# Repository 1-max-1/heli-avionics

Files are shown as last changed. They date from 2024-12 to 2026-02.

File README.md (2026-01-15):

# heli-avionics
This repository contains the electronics and software for a flight controller. This controller is designed to run a coaxial helicopter using brushed DC motors. The board contains an rf transciever chip for wireless communication with a remote.

I had to learn alot for this project, as there were several things I had no experience with such as the radio transceiver circuitry. In the end, it turned out well and was very fun to make.

Description

Description

# PCBWay
The PCB was fabricated and assembled by [PCBWay](https://www.pcbway.com/). I’m impressed with how it turned out, and I’ve written a short review below based on my experience working with them.

#### PCB Quality
The finished PCB looks and feels excellent. The boards appear durable and well-made, with solid electrical connectivity throughout. Silkscreen print is sharp and clear, and the overall finish gives off a professional feel.

#### Assembly Quality
Assembly was just as good. All components were placed with precision, aligned nicely with their pads, and the soldering was clean — no excess, no bridges, and everything stayed neatly within the boundaries.

#### Communication & Support
Working with PCBWay was a smooth experience. They were professional and quick to respond to any questions I had. One thing I really appreciated was their communication before making any key decisions. For example:
- They double-checked with me before sourcing alternative components.
- When a part was unavailable, they suggested alternatives instead of just swapping it.
- After assembly, the quality control team contacted me about the orientation of a particular component, just to be sure, as the markings were slightly ambiguous.

#### Pricing & Turnaround
Pricing was fair, especially considering the quality and the support included. Quoting and sourcing components was made easy — PCBWay handled that for me, which saved a lot of time. Once everything was confirmed, shipping was fast and the boards arrived well-packed.

Overall, I'm happy with the result and wouldn’t hesitate to use PCBWay again in future projects. If you’re looking for a PCB manufacturer that’s reliable, responsive, and produces high-quality results — they’re worth checking out.

# Electronics
**Motor drivers**

The system uses three `DRV8212` BDC motor drivers to drive the tail and coaxial propellors. Some analysis shows that these chips should handle the current demands while remaining below maximum safe temperatures.
The motor driver circuit also includes significant bulk capacitance to handle large spikes in motor current.

The first design of the motor driver circuit used 1 driver chip for both motors. However after more testing, I found that the motors drew more current than expected when at full power. This was over the maximum limit of the motor driver chip. Initially, I started looking for replacement chips with better capabilities. However, the options were either too big, unavailable or could not operate at the voltage I wanted. Eventually, I realised this was the wrong way to go about it and decided to have another look at the original drivers. I discovered that if the 2 outputs on the chip were joined together, this would effectively double the maximum current, which was now sufficient for these motors. However, this solution does require 2 driver chips instead of one. I initially had concerns about space on the board, but after many hours of rearranging and rerouting I found a way to fit both parts on the board.

**MCU**

The MCU is an `atmega4808`. Although possibly not the fanciest choice, I selected this one because it's easy to program, I have used it before, and I know how to make it work.

**Programming**

The MCU can be programmed through UPDI or through the USART pins (once the bootloader has been uploaded). These are broken out to pin headers for easy access. The board also includes an external reset line + button.

I have also broken out an I2C line and a spare GPIO to another pin header in case I want to add more things onto the helicopter in the future.

**Radio**

This board includes a rf transceiver: `nrf24l01`. Like the MCU, this is not fancy but there's alot of documentation for it and I'd rather start with something easier because my rf knowledge is limited (for now).
The board contains an impedance matching network to match the transceiver output to 50 ohms. A wire antenna is used because it should give the best range and I dont have space for a PCB antenna or any bulky connectors like SMA. The antenna will also have to be tuned by cutting it to a specific length. I think UC has network analyzers which could help with this...

**Power regulation**

There are two seperate `TPS7A2030` voltage regulators - one for the radio and one for the rest of the circuit. This is done to try and minimize noise on the radio. The MCU also keeps track of the battery voltage through a divider to ensure that it remains at a safe level.

**Sensors**

The board includes a `BMP390` pressure sensor which can be used to determine the altitude of the helicopter.

# Software
TODO

Will use platformIO, c++

# Why?
I found this helicopter in an e-waste center. The remote was missing and the electronics inside of it seemed to be slightly burnt. 

| Description | 
|:--:| 
| *Disassembled helicopter on test stand* |

After taking it apart and relubricating all the shafts and gears, I tested the motors and they still seemed to work fine.
I decided it would be fun to fix it up and make my own controller for it.

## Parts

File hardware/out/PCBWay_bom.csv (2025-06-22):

Designator | Quantity | Value | Footprint | Package | MPN | DNP | Mount_Type | Description | LCSC Part #
C1, C15, C16, C17, C18, C19, C2, C20, C21, C22, C25, C26, C30, C31, C4, C5, C6 | 17 | 22uF | C_0603_1608Metric_Pad1.08x0.95mm_HandSolder |  | CL10A226MQ8NRNC |  | smt | 6.3V 22uF X5R ±20% 0603 Multilayer Ceramic Capacitors MLCC - SMD/SMT ROHS | C59461
C10 | 1 | 2.2nF | C_0603_1608Metric_Pad1.08x0.95mm_HandSolder |  | 0603B222K500NT |  | smt | 50V 2.2nF X7R ±10% 0603 Multilayer Ceramic Capacitors MLCC - SMD/SMT ROHS | C1604
C11, C9 | 2 | 12pF | C_0603_1608Metric_Pad1.08x0.95mm_HandSolder |  | CC0603FRNPO9BN120 |  | smt | 50V 12pF NP0 ±1% 0603 Multilayer Ceramic Capacitors MLCC - SMD/SMT ROHS | C519482
C12 | 1 | 4.7pF | C_0603_1608Metric_Pad1.08x0.95mm_HandSolder |  | 0603CG4R7C500NT |  | smt | 50V 4.7pF C0G 0603 Multilayer Ceramic Capacitors MLCC - SMD/SMT ROHS | C1669
C13 | 1 | 1.5pF | C_0603_1608Metric_Pad1.08x0.95mm_HandSolder |  | HH18N1R5B500CT |  | smt | 1.5 pF ±0.1pF 50V Ceramic Capacitor C0G, NP0 0603 (1608 Metric)
C14 | 1 | 1pF | C_0603_1608Metric_Pad1.08x0.95mm_HandSolder |  | HH18N1R0B500CT |  | smt | 1 pF ±0.1pF 50V Ceramic Capacitor C0G, NP0 0603 (1608 Metric)
C27 | 1 | 1nF | C_0603_1608Metric_Pad1.08x0.95mm_HandSolder |  | CL10B102KB8NNNC | Yes | smt | 50V 1nF X7R ±10% 0603 Multilayer Ceramic Capacitors MLCC - SMD/SMT ROHS | C1588
C28 | 1 | 100nF | C_0603_1608Metric_Pad1.08x0.95mm_HandSolder |  | CC0603KRX7R9BB104 |  | smt | 50V 100nF X7R ±10% 0603 Multilayer Ceramic Capacitors MLCC - SMD/SMT ROHS | C14663
C3 | 1 | 100nF | C_0603_1608Metric_Pad1.08x0.95mm_HandSolder |  | CC0603KRX7R9BB104 | Yes | smt | 50V 100nF X7R ±10% 0603 Multilayer Ceramic Capacitors MLCC - SMD/SMT ROHS | C14663
C7 | 1 | 33nF | C_0603_1608Metric_Pad1.08x0.95mm_HandSolder |  | CL10B333KB8NNNC |  | smt | 50V 33nF X7R ±10% 0603 Multilayer Ceramic Capacitors MLCC - SMD/SMT ROHS | C21117
C8 | 1 | 10nF | C_0603_1608Metric_Pad1.08x0.95mm_HandSolder |  | 0603B103K500NT | Yes | smt | Unpolarized capacitor | C57112
D2 | 1 | NCD0805R1 | LED_0805_2012Metric_Pad1.15x1.40mm_HandSolder |  | NCD0805R1 |  | smt | Red 25mA 67mcd~195mcd -30℃~+85℃ 615nm~630nm Independent Diode Red 130° 65mW 1.6V~2.6V 0805 LED Indication - Discrete ROHS | C84256
L1 | 1 | 2.7nH | L_0603_1608Metric_Pad1.05x0.95mm_HandSolder |  | BSCQ000603032N7B00 |  | smt | 2.7 nH Unshielded Multilayer Inductor 400 mA 320mOhm Max 0201 (0603 Metric)
L2 | 1 | 8.2nH | L_0603_1608Metric_Pad1.05x0.95mm_HandSolder |  | BSCQ000603038N2H00 |  | smt | 8.2 nH Unshielded Multilayer Inductor 290 mA 570mOhm Max 0201 (0603 Metric)
L3 | 1 | 3.9nH | L_0603_1608Metric_Pad1.05x0.95mm_HandSolder |  | BSCQ000603033N9B00 |  | smt | 3.9 nH Unshielded Multilayer Inductor 350 mA 410mOhm Max 0201 (0603 Metric)
Q1 | 1 | AO3400A | SOT-23 |  | AO3400A |  | smt | 30V Vds, 5.7A Id, N-Channel MOSFET, SOT-23 | C20917
R1 | 1 | 33k | R_0603_1608Metric_Pad0.98x0.95mm_HandSolder |  | 0603WAF3302T5E |  | smt | 100mW Thick Film Resistors 75V ±100ppm/℃ ±1% 33kΩ 0603 Chip Resistor - Surface Mount ROHS | C4216
R10 | 1 | 100R | R_0805_2012Metric_Pad1.20x1.40mm_HandSolder |  | 0805W8F1000T5E |  | smt | 125mW Thick Film Resistors 150V ±100ppm/℃ ±1% 100Ω 0805 Chip Resistor - Surface Mount ROHS | C17408
R11 | 1 | 470R | R_0603_1608Metric_Pad0.98x0.95mm_HandSolder |  | 0603WAF4700T5E |  | smt | 100mW Thick Film Resistors 75V ±100ppm/℃ ±1% 470Ω 0603 Chip Resistor - Surface Mount ROHS | C23179
R12, R13 | 2 | 4k7 | R_0603_1608Metric_Pad0.98x0.95mm_HandSolder |  | 0603WAF4701T5E |  | smt | 100mW Thick Film Resistors 75V ±100ppm/℃ ±1% 4.7kΩ 0603 Chip Resistor - Surface Mount ROHS | C23162
R2 | 1 | 330R | R_0603_1608Metric_Pad0.98x0.95mm_HandSolder |  | 0603WAF3300T5E |  | smt | 100mW Thick Film Resistors 75V ±100ppm/℃ ±1% 330Ω 0603 Chip Resistor - Surface Mount ROHS | C23138
R3, R5, R6 | 3 | 22k | R_0603_1608Metric_Pad0.98x0.95mm_HandSolder |  | 0603WAF2202T5E |  | smt | 100mW Thick Film Resistors 75V ±100ppm/℃ ±1% 22kΩ 0603 Chip Resistor - Surface Mount ROHS | C31850
R4 | 1 | 1M | R_0603_1608Metric_Pad0.98x0.95mm_HandSolder |  | 0603WAF1004T5E |  | smt | 100mW Thick Film Resistors 75V ±100ppm/℃ ±1% 1MΩ 0603 Chip Resistor - Surface Mount ROHS | C22935
R7 | 1 | 150R | R_0603_1608Metric_Pad0.98x0.95mm_HandSolder |  | 0603WAF1500T5E |  | smt | 100mW Thick Film Resistors 75V ±100ppm/℃ ±1% 150Ω 0603 Chip Resistor - Surface Mount ROHS | C22808
R8 | 1 | 51k | R_0603_1608Metric_Pad0.98x0.95mm_HandSolder |  | 0603WAF5102T5E |  | smt | 100mW Thick Film Resistors 75V ±100ppm/℃ ±1% 51kΩ 0603 Chip Resistor - Surface Mount ROHS | C23196
R9 | 1 | 68R | R_0805_2012Metric_Pad1.20x1.40mm_HandSolder |  | 0805W8F680JT5E |  | smt | 125mW Thick Film Resistors 150V ±1% ±200ppm/℃ 68Ω 0805 Chip Resistor - Surface Mount ROHS | C17802
SW1 | 1 | Reset | SW_Push_SPST_NO_Alps_SKRK |  | SKRKAEE020 |  | smt | 2.9mm 2mm Round Button 50mA Vertical welding 3.9mm SPST 12V SMD Tactile Switches ROHS | C115357
U1 | 1 | ATmega4808-A | TQFP-32_7x7mm_P0.8mm |  | ATMEGA4808-AFR |  | smt | AVR Microcontroller, 20MHz, 48kB Flash, 6kB SRAM, 256B EEPROM, TQFP-32 | C2052755
U2 | 1 | NRF24L01P | QFN-20-1EP_4x4mm_P0.5mm_EP2.5x2.5mm |  | NRF24L01P-R |  | smt | Ultra low power 2 Mbps 2.4GHz RF Transceiver, QFN-20 | C8791
U3, U4, U8 | 3 | DRV8212 | WSON-8-1EP_2x2mm_P0.5mm_EP0.9x1.6mm_ThermalVias |  | DRV8212DSGR |  | smt | H-Bridge driver, 4A, Low Voltage, PWM input, Half Bridge Mode, Low-Power Sleep Mode, WSON-8 | C2843766
U5 | 1 | BMP390L | BMP390L LGA 2.0x2.0 mm |  | BMP390L |  | smt | 24-bit barometric pressure sensor, low-noise, low-power. | C2684802
U6, U7 | 2 | TPS7A2030PDBV | SOT-23-5_HandSoldering |  | TPS7A2030PDBVR |  | smt | 300-mA Ultra-Low-Noise Low-IQ, High PSRR LDO, 3.0V, SOT-23 | C963429
Y1 | 1 | 16MHz | Crystal_SMD_3225-4Pin_3.2x2.5mm |  | X322516MLB4SI |  | smt | Four pin crystal, 16MHz, X322516MLB4SI | C13738

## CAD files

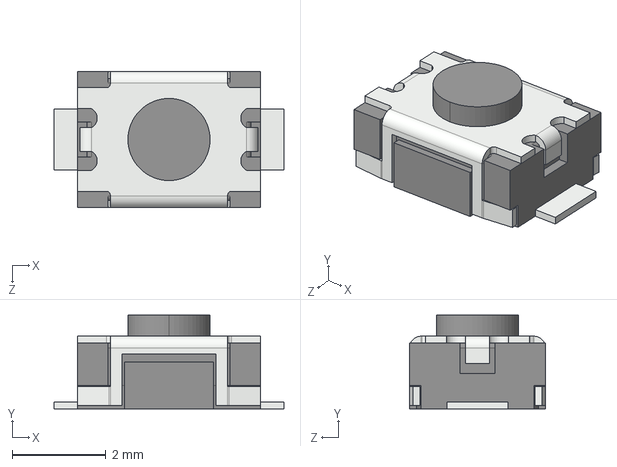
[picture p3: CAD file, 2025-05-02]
hardware/heli-3d-models/User Library-Pushbutton3x4x2.step
4.90 x 2.00 x 2.90 mm

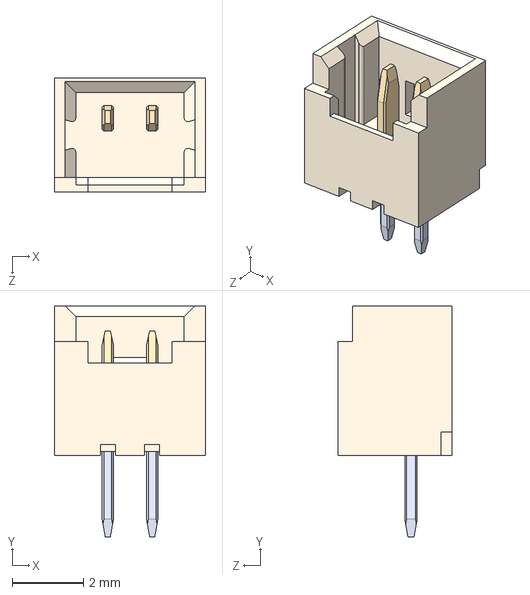
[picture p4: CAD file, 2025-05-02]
hardware/heli-3d-models/molex-picoblade-2pin-1.25mm-pitch.STEP
4.25 x 6.50 x 3.20 mm

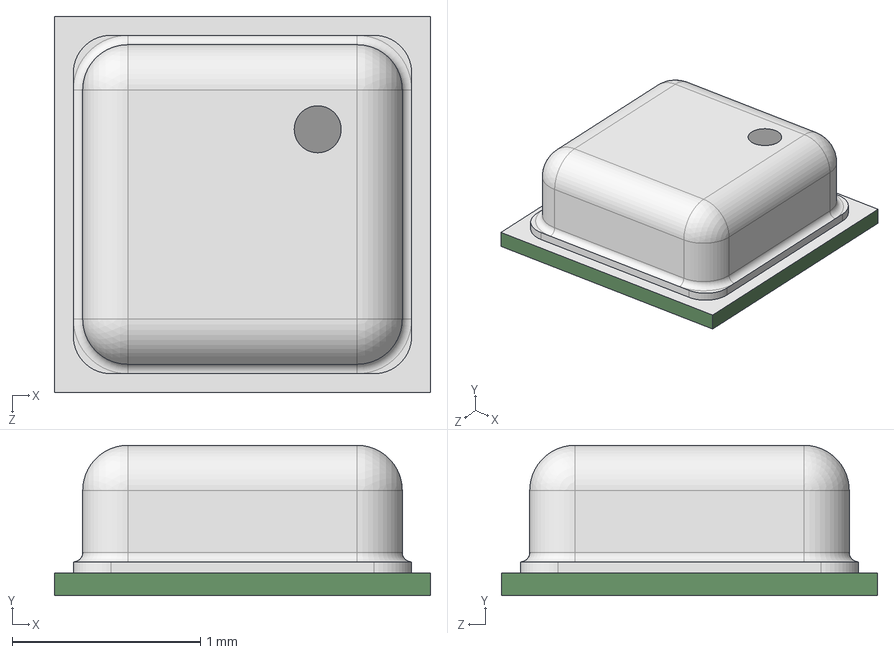
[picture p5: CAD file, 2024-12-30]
hardware/heli-3d-models/BMP390L.step
2.00 x 0.8 x 2.00 mm

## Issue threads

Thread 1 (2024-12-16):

Notes

1-max-1, 2024-12-16:
### MCU
Looking at atmega4809. I have experience with this already, programming it is fairly easy. It has SPI, I2C and PWM so should be good.
Flash size should be enough. Bootloaders are simple. Plenty of decoupling.

### RF
Will be wired to nrf24 chip. Schematic for this can be found in datasheets and there are plenty of examples online, including the PCB antenna and impedance matching network.

### Motor drivers
Brushed, DC, x3. Drive through PWM. Could use motor driver chip, or mosfets directly.

### Altitude sensor
Some kind of pressure sensor, preferably over SPI.

### Battery
Powered by lipo cells, may need 2 to run the motors properly, however nrf24 runs on 3.3v so would need LDO.
Also need battery monitoring system to avoid using the cells when below safe threshold. No onboard battery charging system due to complexity and fire hazard.

1-max-1, 2025-01-15:
TODO:

- [ ] 2x LED's on GPIO pins, not power (always on) because waste of current. Maybe one on the bootloader pin.
- [ ] Check pin order on connectors
- [ ] Check footprints and pin order on all components
- [ ] UART programming
- [ ] Spare exposed GPIO and SPI
- [ ] Exposed pad/hole for additional decoupling to be added if needed.
- [ ] Antenna

1-max-1, 2025-05-31:
### RF components
**1.5pF cap**
LCSC: [C3869699](https://www.lcsc.com/product-detail/Multilayer-Ceramic-Capacitors-MLCC-SMD-SMT_Murata-Electronics-GQM1875C2E1R5BB12D_C3869699.html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)

**1 pF cap**
LCSC: [C2178951](https://www.lcsc.com/product-detail/Multilayer-Ceramic-Capacitors-MLCC-SMD-SMT_Murata-Electronics-GQM1875C2E1R0BB12D_C2178951.html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)

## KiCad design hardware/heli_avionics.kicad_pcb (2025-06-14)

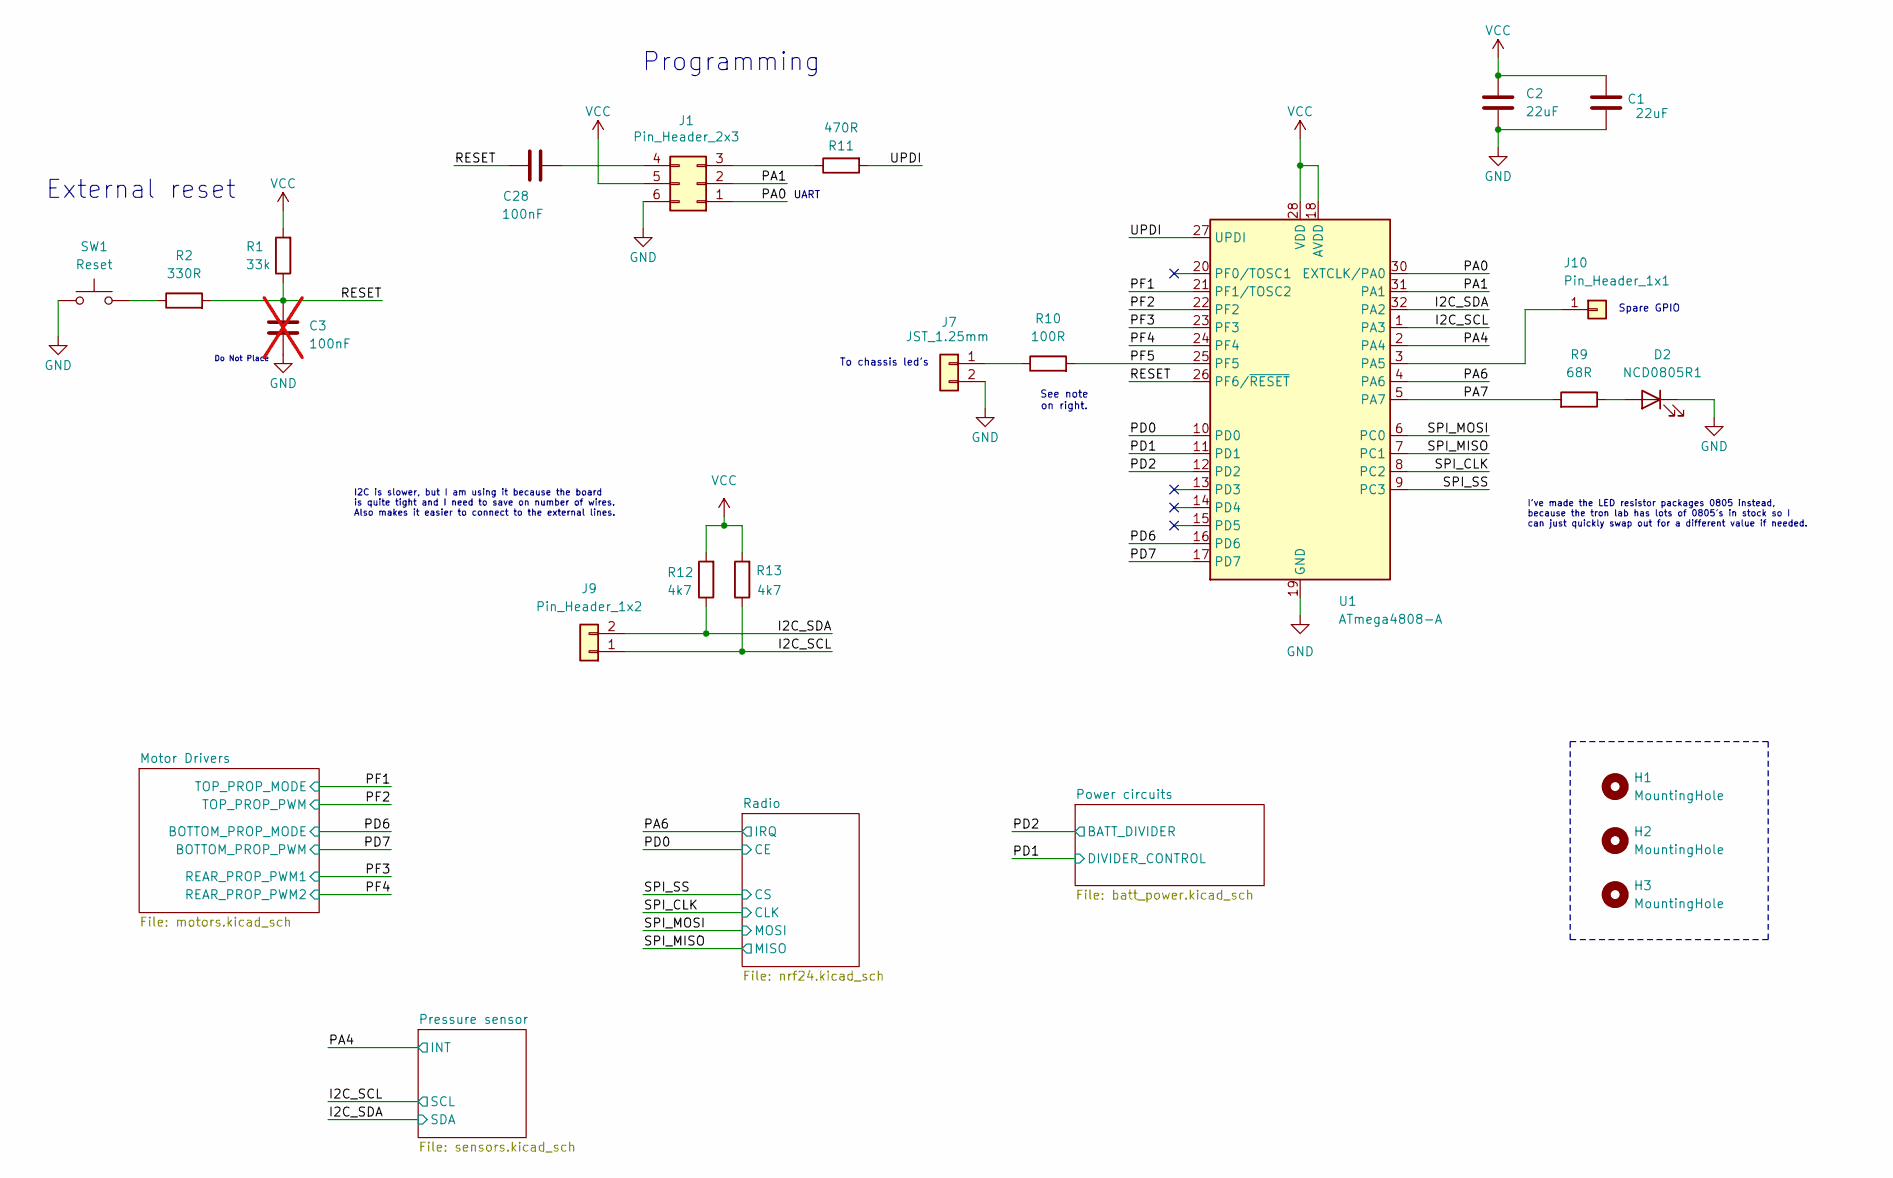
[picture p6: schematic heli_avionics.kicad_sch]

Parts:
C1, C2: 22uF; C_0603_1608Metric_Pad1.08x0.95mm_HandSolder; MPN CL10A226MQ8NRNC; LCSC Part # C59461
C3: 100nF; C_0603_1608Metric_Pad1.08x0.95mm_HandSolder; MPN CC0603KRX7R9BB104; LCSC Part # C14663; not fitted
C28: 100nF; C_0603_1608Metric_Pad1.08x0.95mm_HandSolder; MPN CC0603KRX7R9BB104; LCSC Part # C14663
D2: NCD0805R1; LED_0805_2012Metric_Pad1.15x1.40mm_HandSolder; MPN NCD0805R1; LCSC Part # C84256
H1, H2, H3: MountingHole; MountingHole_2mm
J1: Pin_Header_2x3; PinHeader_2x03_P2.54mm_Vertical
J7: JST_1.25mm; Molex_PicoBlade_53047-0210_1x02_P1.25mm_Vertical
J9: Pin_Header_1x2; PinHeader_1x02_P2.54mm_Vertical
J10: Pin_Header_1x1; PinHeader_1x01_P2.54mm_Vertical
R1: 33k; R_0603_1608Metric_Pad0.98x0.95mm_HandSolder; MPN 0603WAF3302T5E; LCSC Part # C4216
R2: 330R; R_0603_1608Metric_Pad0.98x0.95mm_HandSolder; MPN 0603WAF3300T5E; LCSC Part # C23138
R9: 68R; R_0805_2012Metric_Pad1.20x1.40mm_HandSolder; MPN 0805W8F680JT5E; LCSC Part # C17802
R10: 100R; R_0805_2012Metric_Pad1.20x1.40mm_HandSolder; MPN 0805W8F1000T5E; LCSC Part # C17408
R11: 470R; R_0603_1608Metric_Pad0.98x0.95mm_HandSolder; MPN 0603WAF4700T5E; LCSC Part # C23179
R12, R13: 4k7; R_0603_1608Metric_Pad0.98x0.95mm_HandSolder; MPN 0603WAF4701T5E; LCSC Part # C23162
SW1: Reset; SW_Push_SPST_NO_Alps_SKRK; MPN SKRKAEE020; LCSC Part # C115357
U1: ATmega4808-A; TQFP-32_7x7mm_P0.8mm; MPN ATMEGA4808-AFR; LCSC Part # C2052755

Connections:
/I2C_SCL: J9.1, R13.1, U1.1 (PA3); also elsewhere on the board
/I2C_SDA: J9.2, R12.1, U1.32 (PA2); also elsewhere on the board
/PA0: J1.1, U1.30 (EXTCLK/PA0)
/PA1: J1.2, U1.31 (PA1)
/PA4: U1.2 (PA4); also elsewhere on the board
/PA6: U1.4 (PA6); also elsewhere on the board
/PA7: R9.2, U1.5 (PA7)
/PD0: U1.10 (PD0); also elsewhere on the board
/PD1: U1.11 (PD1); also elsewhere on the board
/PD2: U1.12 (PD2); also elsewhere on the board
/PD6: U1.16 (PD6); also elsewhere on the board
/PD7: U1.17 (PD7); also elsewhere on the board
/PF1: U1.21 (PF1/TOSC2); also elsewhere on the board
/PF2: U1.22 (PF2); also elsewhere on the board
/PF3: U1.23 (PF3); also elsewhere on the board
/PF4: U1.24 (PF4); also elsewhere on the board
/PF5: R10.2, U1.25 (PF5)
/RESET: C3.1, C28.1, R1.1, R2.2, U1.26 (PF6/~RESET)
/SPI_CLK: U1.8 (PC2); also elsewhere on the board
/SPI_MISO: U1.7 (PC1); also elsewhere on the board
/SPI_MOSI: U1.6 (PC0); also elsewhere on the board
/SPI_SS: U1.9 (PC3); also elsewhere on the board
/UPDI: R11.2, U1.27 (UPDI)
GND: C1.2, C2.2, C3.2, D2.1 (K), J1.6, J7.2, SW1.1, U1.19 (GND), U1.29 (GND); also elsewhere on the board
unnamed: D2.2 (A), R9.1
unnamed: J1.3, R11.1
unnamed: C28.2, J1.4
unnamed: J7.1, R10.1
unnamed: J10.1, U1.3 (PA5)
unnamed: R2.1, SW1.2
VCC: C1.1, C2.1, J1.5, R1.2, R12.2, R13.2, U1.18 (AVDD), U1.28 (VDD); also elsewhere on the board

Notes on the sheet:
Do Not Place
I've made the LED resistor packages 0805 instead, because the tron lab has lots of 0805's in stock so I can just quickly swap out for a different value if needed.
I2C is slower, but I am using it because the board is quite tight and I need to save on number of wires. Also makes it easier to connect to the external lines.
UART
See note on right.
To chassis led's
Spare GPIO
Programming
External reset

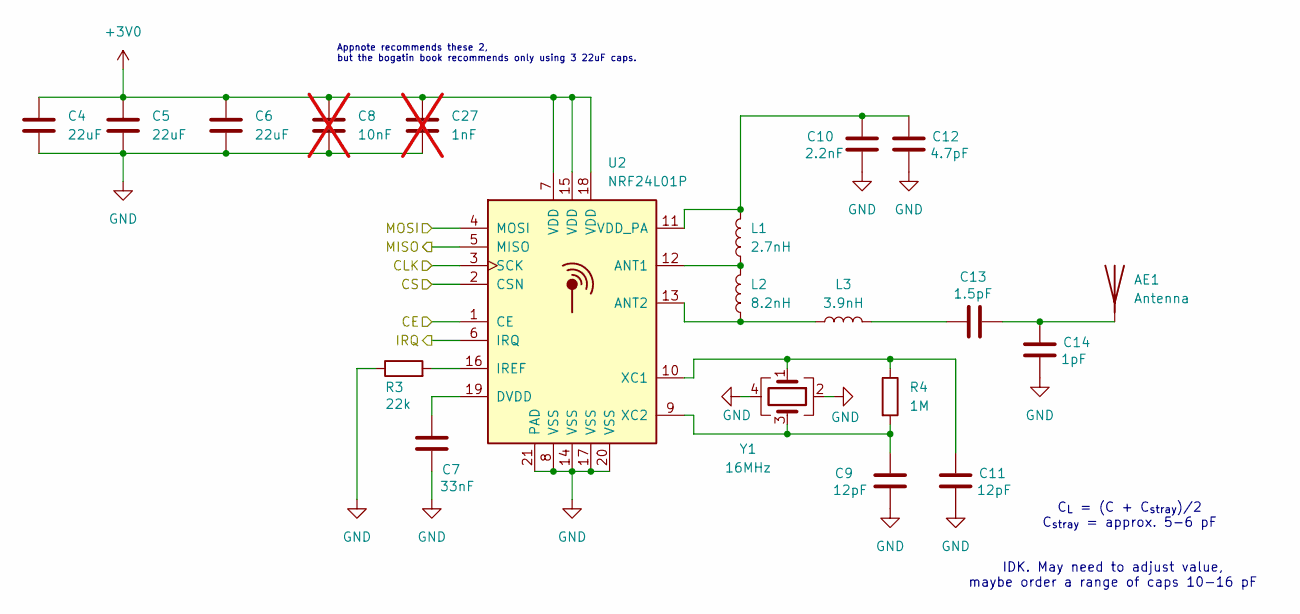
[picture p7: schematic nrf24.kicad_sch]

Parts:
AE1: Antenna; SolderWire-0.5sqmm_1x01_D0.9mm_OD2.1mm
C4, C5, C6: 22uF; C_0603_1608Metric_Pad1.08x0.95mm_HandSolder; MPN CL10A226MQ8NRNC; LCSC Part # C59461
C7: 33nF; C_0603_1608Metric_Pad1.08x0.95mm_HandSolder; MPN CL10B333KB8NNNC; LCSC Part # C21117
C8: 10nF; C_0603_1608Metric_Pad1.08x0.95mm_HandSolder; MPN 0603B103K500NT; LCSC Part # C57112; not fitted
C9, C11: 12pF; C_0603_1608Metric_Pad1.08x0.95mm_HandSolder; MPN CC0603FRNPO9BN120; LCSC Part # C519482
C10: 2.2nF; C_0603_1608Metric_Pad1.08x0.95mm_HandSolder; MPN 0603B222K500NT; LCSC Part # C1604
C12: 4.7pF; C_0603_1608Metric_Pad1.08x0.95mm_HandSolder; MPN 0603CG4R7C500NT; LCSC Part # C1669
C13: 1.5pF; C_0603_1608Metric_Pad1.08x0.95mm_HandSolder; MPN HH18N1R5B500CT
C14: 1pF; C_0603_1608Metric_Pad1.08x0.95mm_HandSolder; MPN HH18N1R0B500CT
C27: 1nF; C_0603_1608Metric_Pad1.08x0.95mm_HandSolder; MPN CL10B102KB8NNNC; LCSC Part # C1588; not fitted
L1: 2.7nH; L_0603_1608Metric_Pad1.05x0.95mm_HandSolder; MPN BSCQ000603032N7B00
L2: 8.2nH; L_0603_1608Metric_Pad1.05x0.95mm_HandSolder; MPN BSCQ000603038N2H00
L3: 3.9nH; L_0603_1608Metric_Pad1.05x0.95mm_HandSolder; MPN BSCQ000603033N9B00
R3: 22k; R_0603_1608Metric_Pad0.98x0.95mm_HandSolder; MPN 0603WAF2202T5E; LCSC Part # C31850
R4: 1M; R_0603_1608Metric_Pad0.98x0.95mm_HandSolder; MPN 0603WAF1004T5E; LCSC Part # C22935
U2: NRF24L01P; NRF24L01_HandSolder_SpecialPad; MPN NRF24L01P-R; LCSC Part # C8791
Y1: 16MHz; Crystal_SMD_3225-4Pin_3.2x2.5mm; MPN X322516MLB4SI; LCSC Part # C13738

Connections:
+3V0: C4.1, C5.1, C6.1, C8.1, C27.1, U2.7 (VDD), U2.15 (VDD), U2.18 (VDD); also elsewhere on the board
/PA6: U2.6 (IRQ); also elsewhere on the board
/PD0: U2.1 (CE); also elsewhere on the board
/SPI_CLK: U2.3 (SCK); also elsewhere on the board
/SPI_MISO: U2.5 (MISO); also elsewhere on the board
/SPI_MOSI: U2.4 (MOSI); also elsewhere on the board
/SPI_SS: U2.2 (CSN); also elsewhere on the board
GND: C4.2, C5.2, C6.2, C7.2, C8.2, C9.2, C10.2, C11.2, C12.2, C14.2, C27.2, R3.1, U2.8 (VSS), U2.14 (VSS), U2.17 (VSS), U2.20 (VSS), U2.21 (PAD), Y1.2, Y1.4; also elsewhere on the board
unnamed: AE1.1 (A), C13.2, C14.1
unnamed: C13.1, L3.2
unnamed: L1.1, L2.2, U2.12 (ANT1)
unnamed: L2.1, L3.1, U2.13 (ANT2)
unnamed: C7.1, U2.19 (DVDD)
unnamed: R3.2, U2.16 (IREF)
unnamed: C10.1, C12.1, L1.2, U2.11 (VDD_PA)
unnamed: C11.1, R4.1, U2.10 (XC1), Y1.1
unnamed: C9.1, R4.2, U2.9 (XC2), Y1.3

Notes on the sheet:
C_{L} = (C + C_{stray})/2 C_{stray} = approx. 5-6 pF
Appnote recommends these 2, but the bogatin book recommends only using 3 22uF caps.
IDK. May need to adjust value, maybe order a range of caps 10-16 pF

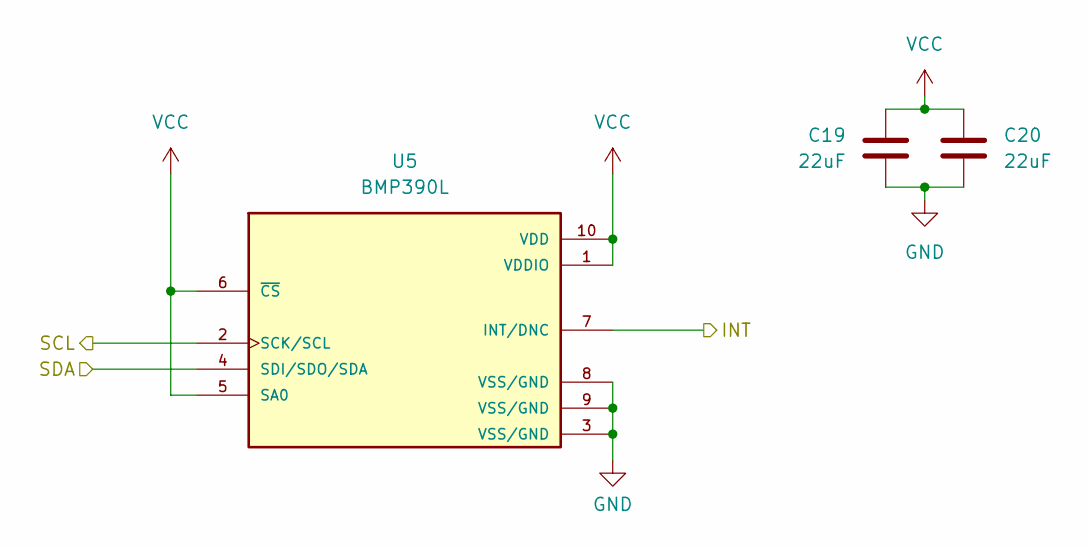
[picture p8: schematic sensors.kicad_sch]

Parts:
C19, C20: 22uF; C_0603_1608Metric_Pad1.08x0.95mm_HandSolder; MPN CL10A226MQ8NRNC; LCSC Part # C59461
U5: BMP390L; MPN BMP390L; LCSC Part # C2684802

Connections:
/I2C_SCL: U5.2 (SCK/SCL); also elsewhere on the board
/I2C_SDA: U5.4 (SDI/SDO/SDA); also elsewhere on the board
/PA4: U5.7 (INT/DNC); also elsewhere on the board
GND: C19.2, C20.2, U5.3 (VSS/GND), U5.8 (VSS/GND), U5.9 (VSS/GND); also elsewhere on the board
VCC: C19.1, C20.1, U5.1 (VDDIO), U5.5 (SA0), U5.6 (~CS), U5.10 (VDD); also elsewhere on the board

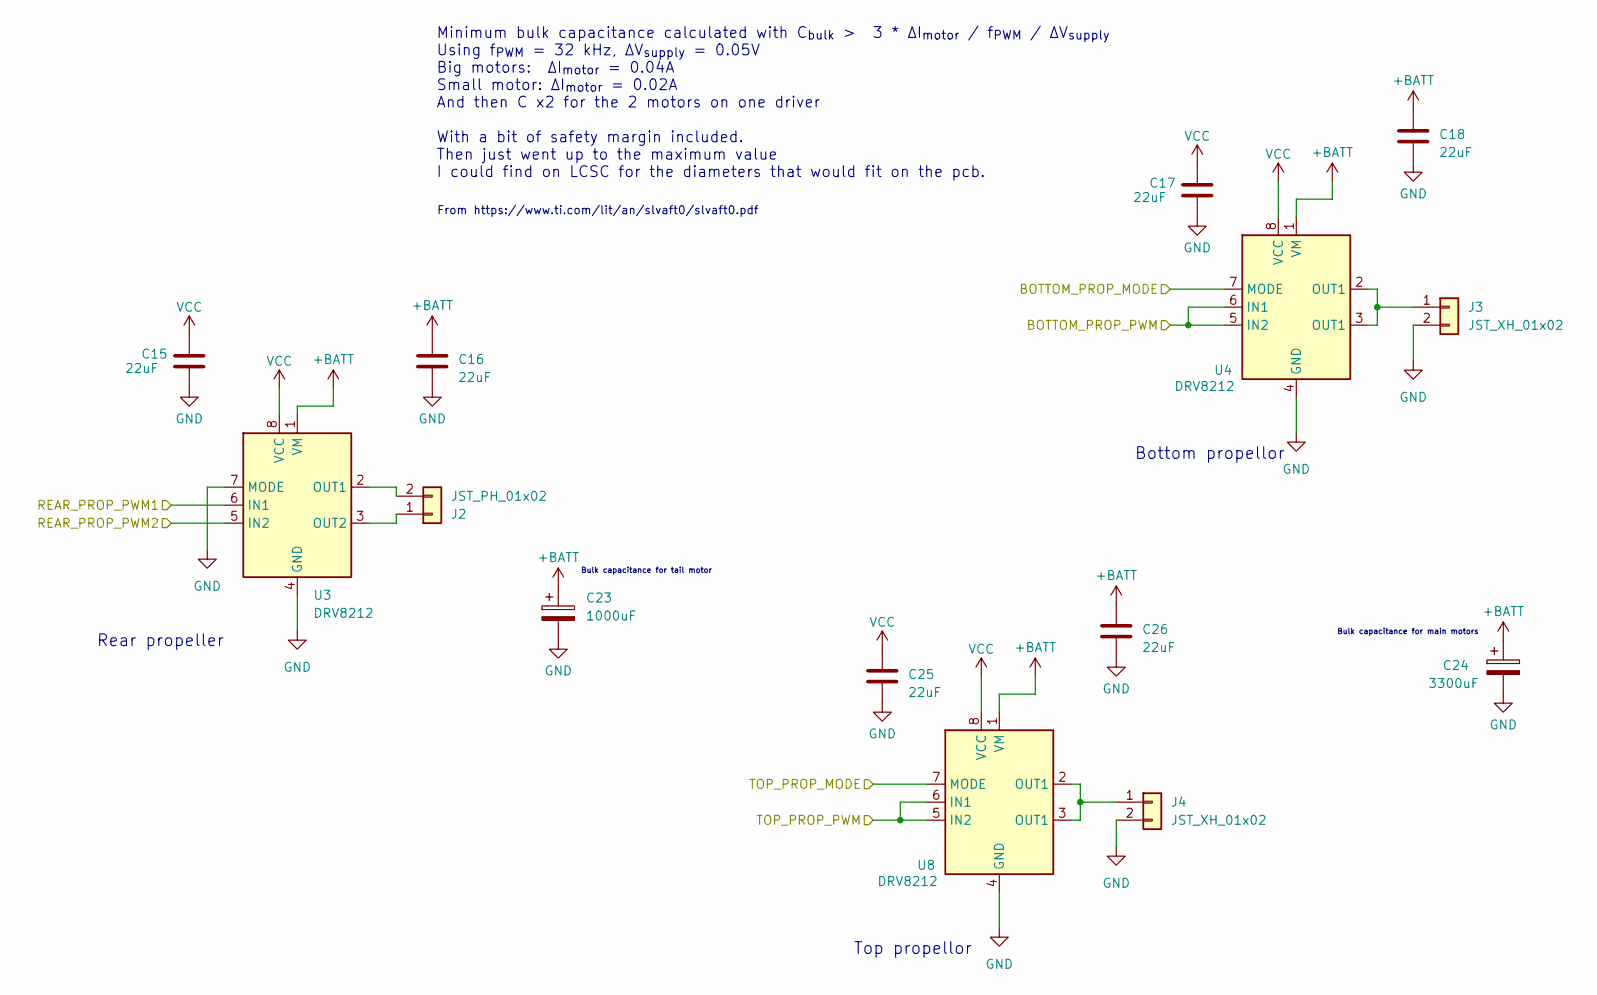
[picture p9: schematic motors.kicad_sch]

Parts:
C15, C16, C17, C18, C25, C26: 22uF; C_0603_1608Metric_Pad1.08x0.95mm_HandSolder; MPN CL10A226MQ8NRNC; LCSC Part # C59461
C23: 1000uF; CP_Radial_D6.3mm_P2.50mm; MPN SPT1AM102E14ORVZC; LCSC Part # C3024245
C24: 3300uF; CP_Radial_D10.0mm_P5.00mm; MPN RL1A332MG250A00CE0; LCSC Part # C240437
J2: JST_PH_01x02; JST_PH_B2B-PH-K_1x02_P2.00mm_Vertical
J3, J4: JST_XH_01x02; JST_XH_B2B-XH-A_1x02_P2.50mm_Vertical
U3, U4, U8: DRV8212; WSON-8-1EP_2x2mm_P0.5mm_EP0.9x1.6mm_ThermalVias; MPN DRV8212DSGR; LCSC Part # C2843766

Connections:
+BATT: C16.1, C18.1, C23.1, C24.1, C26.1, U3.1 (VM), U4.1 (VM), U8.1 (VM); also elsewhere on the board
/PD6: U4.7 (MODE); also elsewhere on the board
/PD7: U4.5 (IN2), U4.6 (IN1); also elsewhere on the board
/PF1: U8.7 (MODE); also elsewhere on the board
/PF2: U8.5 (IN2), U8.6 (IN1); also elsewhere on the board
/PF3: U3.6 (IN1); also elsewhere on the board
/PF4: U3.5 (IN2); also elsewhere on the board
GND: C15.2, C16.2, C17.2, C18.2, C23.2, C24.2, C25.2, C26.2, J3.2, J4.2, U3.4 (GND), U3.7 (MODE), U3.9 (GND), U4.4 (GND), U4.9 (GND), U8.4 (GND), U8.9 (GND); also elsewhere on the board
unnamed: J2.1, U3.3 (OUT2)
unnamed: J2.2, U3.2 (OUT1)
unnamed: J3.1, U4.2 (OUT1), U4.3 (OUT1)
unnamed: J4.1, U8.2 (OUT1), U8.3 (OUT1)
VCC: C15.1, C17.1, C25.1, U3.8 (VCC), U4.8 (VCC), U8.8 (VCC); also elsewhere on the board

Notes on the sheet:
Top propellor
Rear propeller
Minimum bulk capacitance calculated with C_{bulk} > 3 * ∆I_{motor} / f_{PWM} / ∆V_{supply} Using f_{PWM} = 32 kHz, ∆V_{supply} = 0.05V Big motors: ∆I_{motor} = 0.04A Small motor: ∆I_{motor} = 0.02A And then C x2 for the 2 motors on one driver With a bit of safety margin included. Then just went up 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
From https://www.ti.com/lit/an/slvaft0/slvaft0.pdf
Bulk capacitance for tail motor
Bottom propellor
Bulk capacitance for main motors

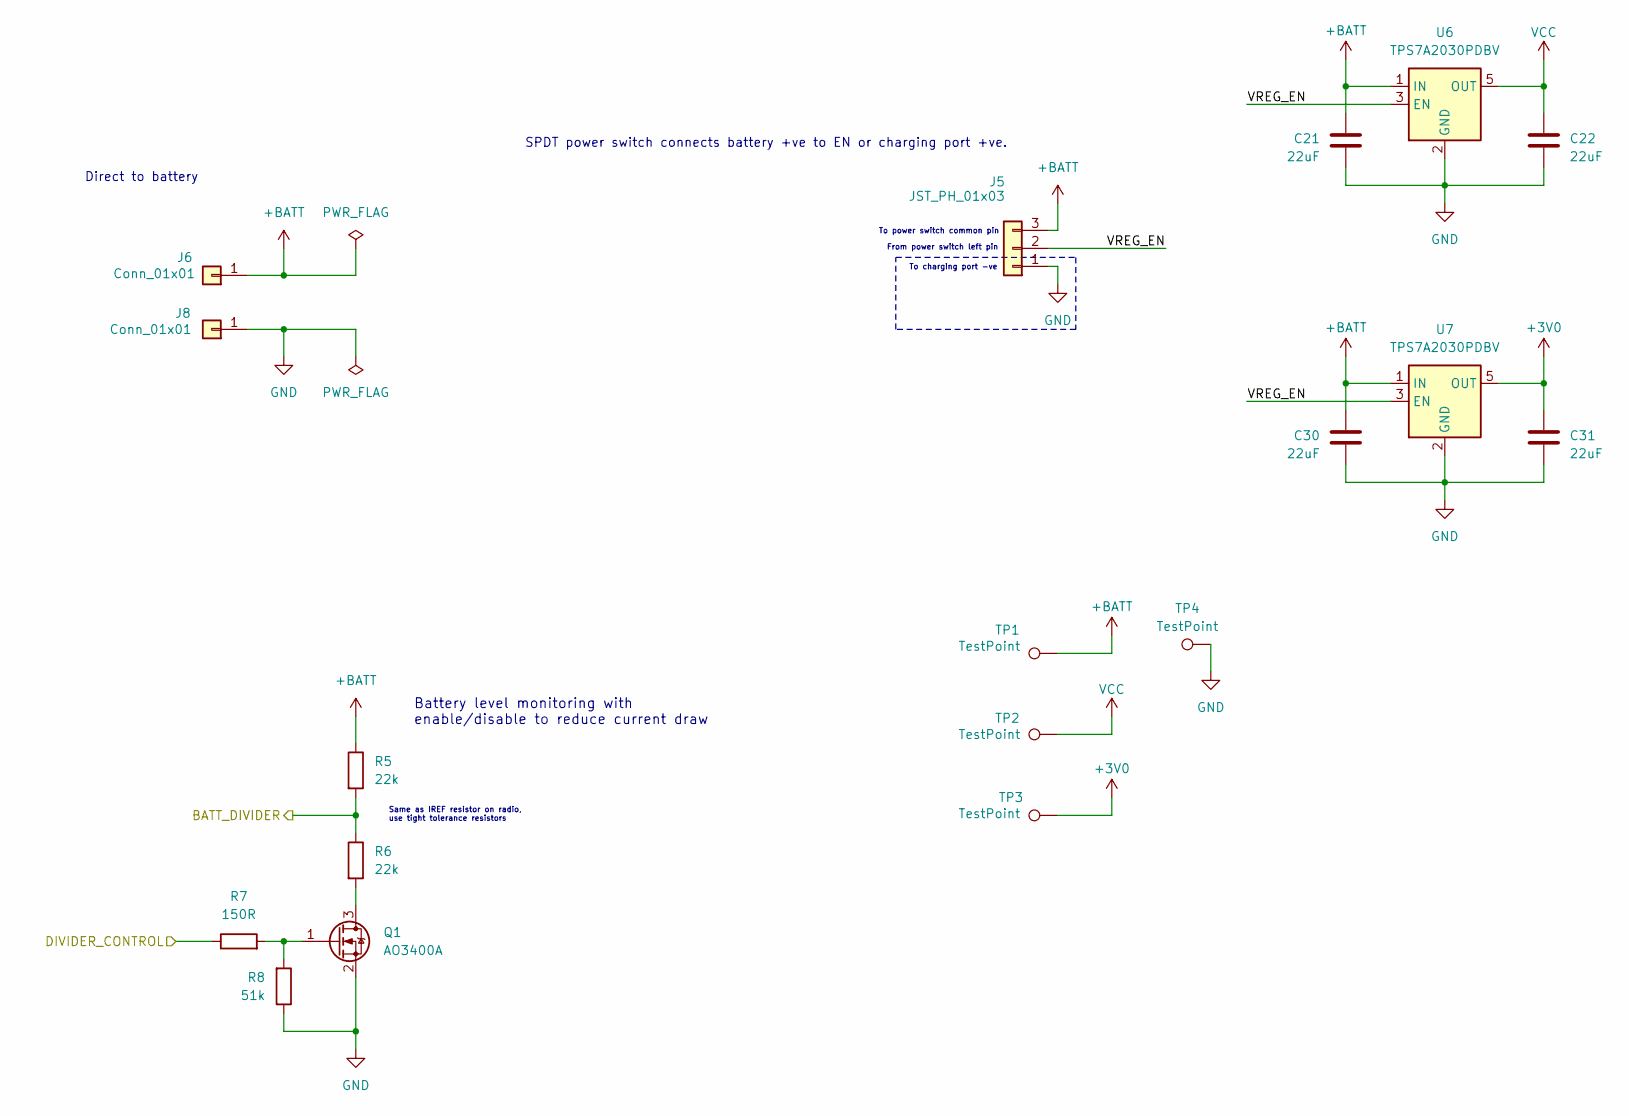
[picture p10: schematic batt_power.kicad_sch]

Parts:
C21, C22, C30, C31: 22uF; C_0603_1608Metric_Pad1.08x0.95mm_HandSolder; MPN CL10A226MQ8NRNC; LCSC Part # C59461
J5: JST_PH_01x03; JST_PH_B3B-PH-K_1x03_P2.00mm_Vertical
J6, J8: Conn_01x01; SolderWire-1sqmm_1x01_D1.4mm_OD3.9mm
Q1: AO3400A; SOT-23; MPN AO3400A; LCSC Part # C20917
R5, R6: 22k; R_0603_1608Metric_Pad0.98x0.95mm_HandSolder; MPN 0603WAF2202T5E; LCSC Part # C31850
R7: 150R; R_0603_1608Metric_Pad0.98x0.95mm_HandSolder; MPN 0603WAF1500T5E; LCSC Part # C22808
R8: 51k; R_0603_1608Metric_Pad0.98x0.95mm_HandSolder; MPN 0603WAF5102T5E; LCSC Part # C23196
TP1, TP3: TestPoint; TestPoint_Pad_1.5x1.5mm
TP2, TP4: TestPoint; TestPoint_Pad_D1.5mm
U6, U7: TPS7A2030PDBV; SOT-23-5_HandSoldering; MPN TPS7A2030PDBVR; LCSC Part # C963429

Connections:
+3V0: C31.1, TP3.1, U7.5 (OUT); also elsewhere on the board
+BATT: C21.1, C30.1, J5.3, J6.1, R5.1, TP1.1, U6.1 (IN), U7.1 (IN); also elsewhere on the board
/PD1: R7.1; also elsewhere on the board
/PD2: R5.2, R6.1; also elsewhere on the board
/Power circuits/VREG_EN: J5.2, U6.3 (EN), U7.3 (EN)
GND: C21.2, C22.2, C30.2, C31.2, J5.1, J8.1, Q1.2 (S), R8.1, TP4.1, U6.2 (GND), U7.2 (GND); also elsewhere on the board
unnamed: Q1.3 (D), R6.2
unnamed: Q1.1 (G), R7.2, R8.2
VCC: C22.1, TP2.1, U6.5 (OUT); also elsewhere on the board

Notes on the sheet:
To charging port -ve
Direct to battery
From power switch left pin
Same as IREF resistor on radio, use tight tolerance resistors
Battery level monitoring with enable/disable to reduce current draw
To power switch common pin
SPDT power switch connects battery +ve to EN or charging port +ve.

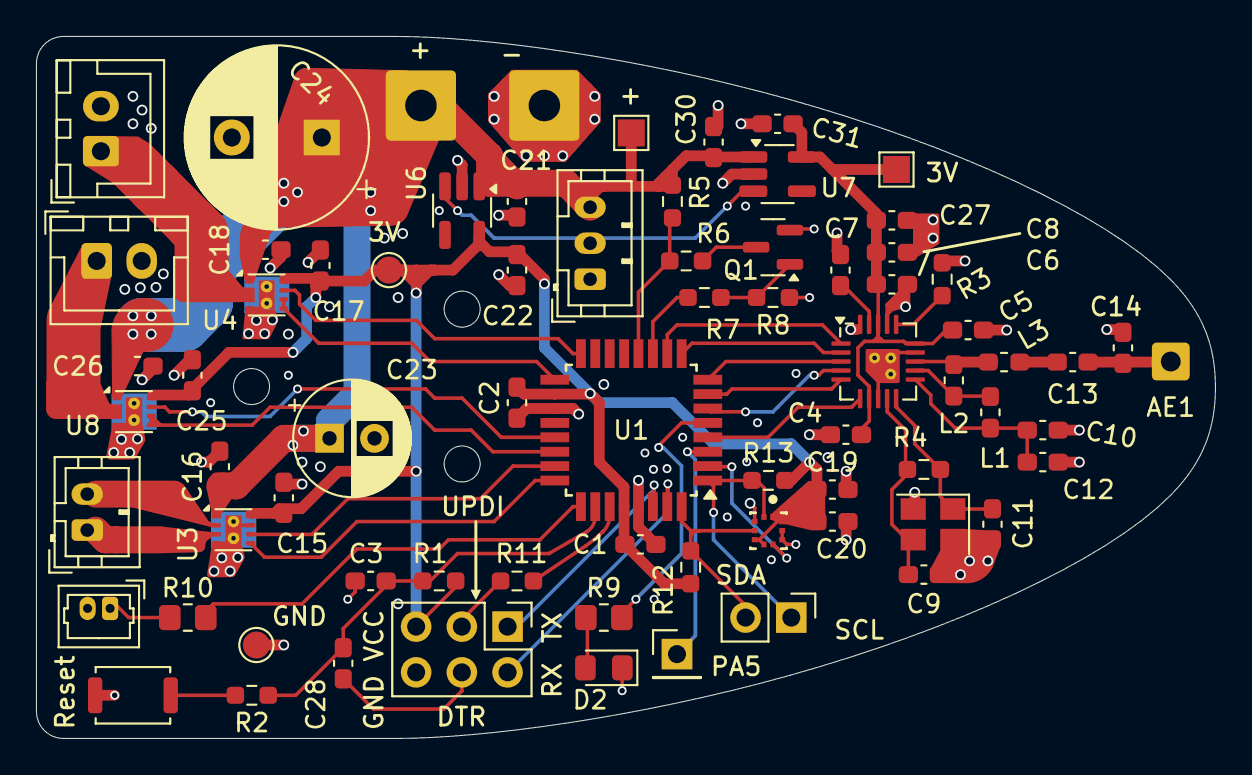
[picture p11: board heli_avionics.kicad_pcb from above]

Board: 4 copper layers, 65.5 x 39.0 mm, 76 parts (0 on the bottom side), 49 nets.

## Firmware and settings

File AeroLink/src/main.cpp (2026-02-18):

#include <Arduino.h>
#include <NimBLEDevice.h>
#include <RF24.h>
#include <string>

constexpr const char* SERVICE_UUID = "aff07927-a273-4b20-bb24-09962b9f950f";
constexpr const char* THROTTLE_CHAR_UUID = "56ce2749-1034-4cc3-8aa5-923399a45243";
constexpr const char* TELEMETRY_CHAR_UUID = "e74ac0ce-8e5b-43c2-bff4-f79bc7557d0d";

constexpr rf24_gpio_pin_t cePin = 21;
constexpr rf24_gpio_pin_t csPin = 5;
//constexpr rf24_gpio_pin_t irqPin = PIN_PA6;

// Addresses chosen not to conflict with preamble, and to have more than one level change
// https://maniacalbits.blogspot.com/2013/04/rf24-addressing-nrf24l01-radios-require.html
constexpr uint8_t addressWidth = 5;
const uint8_t rxAddress[addressWidth] = { 0xf5, 0xd4, 0xba, 0x5c, 0x61 }; // Address of dispatcher
const uint8_t txAddress[addressWidth] = { 0xf5, 0xc5, 0x1e, 0x9c, 0x2d }; // Address of heli radio reading pipe

class CharacteristicCallbacks : public NimBLECharacteristicCallbacks {
	void onWrite(NimBLECharacteristic* pCharacteristic, NimBLEConnInfo& conn) override {
		NimBLEAttValue value = pCharacteristic->getValue();

		if (value.length() > 0) {
			/*radio.stopListening();
			radio.write(value.data(), value.length(), true);
			radio.startListening();*/
			Serial.print("Received some data: ");
			Serial.println(value.c_str());
		}
	}
};

RF24 radio(cePin, csPin);
NimBLECharacteristic* telemetryChar;

bool initBLE() {
	NimBLEDevice::init("AeroLink");
	//NimBLEDevice::setPower(ESP_PWR_LVL_P9);  // Max power

	NimBLEServer* server = NimBLEDevice::createServer();
	NimBLEService* aeroLinkService = server->createService(SERVICE_UUID);

	NimBLECharacteristic* throttleChar = aeroLinkService->createCharacteristic(THROTTLE_CHAR_UUID, NIMBLE_PROPERTY::WRITE_NR);
	throttleChar->setCallbacks(new CharacteristicCallbacks());

	telemetryChar = aeroLinkService->createCharacteristic(TELEMETRY_CHAR_UUID, NIMBLE_PROPERTY::READ | NIMBLE_PROPERTY::NOTIFY);
	
	if (!aeroLinkService->start())
		return false;
	
	NimBLEAdvertising* pAdvertising = NimBLEDevice::getAdvertising();
	if (!pAdvertising->addServiceUUID(SERVICE_UUID))
		return false;
	if (!pAdvertising->setName("AeroLink"))
		return false;
	if (!pAdvertising->start())
		return false;

	return true;
}

bool initRadio() {
	// This will also initialize the SPI bus
	if (!radio.begin())
		return false;

	radio.setAddressWidth(addressWidth);
	//radio.setChannel(40); // TODO: use channel with lowest traffic in my area
	radio.setPALevel(rf24_pa_dbm_e::RF24_PA_LOW);
	radio.enableDynamicPayloads();
	radio.enableDynamicAck();
	radio.disableAckPayload();
	radio.setAutoAck(true);
	radio.setRetries(0, 5);
	radio.setCRCLength(rf24_crclength_e::RF24_CRC_8);

	const bool success = radio.setDataRate(rf24_datarate_e::RF24_1MBPS); // only 1mpbs but we get better signal strength
	if (!success)
		return false;

	// Initial one time setup of transmit address so we can save on SPI traffic later
	radio.stopListening(txAddress);

	// NOTE: most of radio time is spent in receive mode

	radio.openReadingPipe(1, rxAddress);
	radio.startListening();
	return true;
}

void setup() {
	Serial.begin(115200);

	bool success = initBLE();
	
	//initRadio();
}

unsigned long last = 0;

void loop() {
	delay(10);

	unsigned long now = millis();
	if (now - last >= 800) {
		telemetryChar->setValue(std::to_string(now));
		telemetryChar->notify();
		last = now;
	}
}

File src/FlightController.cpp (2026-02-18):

#include "FlightController.h"
#include "tasks.h"
#include <Arduino.h>

void FlightController::setup() {
	Serial.begin(9600);
	Serial.println("Hello there");
	Serial.println((unsigned long)sizeof(unsigned int));
	Serial.println((unsigned long)sizeof(unsigned long));
	Serial.println((unsigned long)sizeof(unsigned long long));
	Serial.println((unsigned long)sizeof(uint16_t));
	Serial.println((unsigned long)sizeof(uint32_t));
	Serial.println((unsigned long)sizeof(int32_t));

	altimeter.init();
	radio.init();
}

void FlightController::loop() {
	const uint32_t curTime = micros();

	// Time triggered scheduling, and only running the task if the current state allows it
	for (Task& task : tasks) {
		if ((task.stateMask & static_cast<uint32_t>(currentState)) == 0)
			continue;

		if (curTime - task.timeOfLastExecution > task.period) {
			task.timeOfLastExecution = curTime;
			(this->*task.execute)();
		}
	}
}

void FlightController::swapState(HeliState newState) {
	currentState = newState;
}

void FlightController::oneSecondTaskAdapter() {
	HeliTasks::oneSecondTask(radio);
}

void FlightController::threePerSecondTaskAdapter() {
	HeliTasks::threePerSecondTask(altimeter);
}

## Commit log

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2024-12-26 Added basic connections for MCU
    [heli_avionics.kicad_sch]
2024-12-26 Added basic connections for nrf24
    [heli_avionics.kicad_sch]
2024-12-27 Basic connections for motor drivers
    [heli_avionics.kicad_sch]
2024-12-30 Added basic connections for pressure sensor
    [BMP390L.step, heli_avionics.kicad_sch]
2024-12-30 Basic connections for voltage regulator
    [heli_avionics.kicad_sch]
2025-01-03 Finish motor driver circuits and move to subsheet
    [heli_avionics.kicad_sch, motors.kicad_sch]
2025-01-04 Complete pressure sensor circuit
    [heli_avionics.kicad_sch]
2025-01-10 Moved radio circuit to subsheet
    [heli_avionics.kicad_sch, nrf24.kicad_sch]
2025-01-16 Created subsheet for power circuits
    [batt_power.kicad_sch, heli_avionics.kicad_sch]
2025-01-16 Tidy net names & move BMP390 to subsheet
    [batt_power.kicad_sch, heli_avionics.kicad_sch, sensors.kicad_sch]
2025-01-16 Added UART and LED
    [heli_avionics.kicad_sch, sensors.kicad_sch]
2025-01-20 Added chassis LED connector
    [heli_avionics.kicad_sch, sensors.kicad_sch]
2025-01-21 Updated values to be in standard series
    [batt_power.kicad_sch, motors.kicad_sch, sensors.kicad_sch]
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2025-01-24 Updated footprints for the IC's
    [batt_power.kicad_sch, heli_avionics.kicad_sch, nrf24.kicad_sch]
2025-01-24 Assigned footprints for connectors
    [batt_power.kicad_sch, heli_avionics.kicad_sch, motors.kicad_sch]
2025-01-27 Misc small
    Remove ESD diode
    Add resistor to UPDI line
    Fix LED resistor
    Assign LED footprint
    [heli_avionics.kicad_sch]
2025-01-27 Assigned footprint for mosfet
    [batt_power.kicad_sch]
2025-01-28 Assigned footprint for crystal and button, fixed gitignore
    [heli_avionics.kicad_sch, nrf24.kicad_sch]
2025-02-10 Added mounting holes and did board outline
    Also tried an initial layout with some components
    [heli_avionics.kicad_pcb, heli_avionics.kicad_sch]
2025-02-10 Assigned footprints for capacitors and inductors
    [batt_power.kicad_sch, heli_avionics.kicad_sch, motors.kicad_sch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]
2025-02-10 Corrected pin order on JST connectors
    [batt_power.kicad_sch, heli_avionics.kicad_sch, motors.kicad_sch]
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2025-02-12 Separated battery connector into 2 different
    [batt_power.kicad_sch]
2025-02-12 Enlarge BMP390 pads and fix silkscreen
    [batt_power.kicad_sch]
2025-02-27 Added separate LDO for NRF24
    [batt_power.kicad_sch, nrf24.kicad_sch]
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2025-02-28 Update board outline and holes
    [heli_avionics.kicad_pcb]
2025-03-08 tryout more layout ideas
    [heli_avionics.kicad_pcb]
2025-03-09 Updated decoupling caps to match guidelines from Eric Bogatin
    [batt_power.kicad_sch, heli_avionics.kicad_sch, motors.kicad_sch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]
2025-03-11 Updated VRM capacitor values
    [batt_power.kicad_sch]
2025-03-12 Setup board properties and design constraints
    Also added some default trace and via sizes
    [heli_avionics.kicad_pcb]
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2025-03-18 New layout idea, savepoint
    Me reckons this is the way to go. Only 1 motor bulk capacitor
    [heli_avionics.kicad_pcb, motors.kicad_sch]
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2025-03-21 Reordered some MCU pin connections for nicer layout
    [heli_avionics.kicad_pcb, heli_avionics.kicad_sch]
2025-04-04 Pressure sensor now uses i2c
    Also rewired nrf24 to use the other SPI
    [heli_avionics.kicad_pcb, heli_avionics.kicad_sch, sensors.kicad_sch]
2025-04-04 Added pin headers for external connections (PA6 and I2C)
    [heli_avionics.kicad_pcb, heli_avionics.kicad_sch]
2025-04-04 Reordered pins on programming connector for cleaner routing
    [heli_avionics.kicad_pcb, heli_avionics.kicad_sch]
2025-04-04 Shifted some things around
    [heli_avionics.kicad_pcb]
2025-04-05 Shifted radio components and testpoints around
    [batt_power.kicad_sch, heli_avionics.kicad_pcb, heli_avionics.kicad_sch]
2025-04-05 Fixed ERC errors
    Had to exclude warning for connecting ground to the bidirectional SA0 pin (pin 5) on the pressure sensor.
    [batt_power.kicad_sch, heli_avionics.kicad_sch]
2025-04-09 Routed most of the radio traces
    [heli_avionics.kicad_pcb]
2025-04-09 Routed most pressure sensor traces
    [heli_avionics.kicad_pcb, sensors.kicad_sch]
2025-04-10 Routed decoupling caps and PWM traces
    [heli_avionics.kicad_pcb]
2025-04-13 Fixed motor driver grounding
    Made new footprint with smaller thermal vias for less solder wicking.
    Added more vias in ground puddle.
    [heli_avionics.kicad_pcb, motors.kicad_sch]
2025-04-13 More signal trace routing and component placement
    [heli_avionics.kicad_pcb]
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2025-04-18 Better motor driver layout
    For the tail motor.
    I believe it to be better, who knows really.
    Although it does have longer PWM signal traces.
    Although the high current motor PWM traces are shorter which is good.
    [heli_avionics.kicad_pcb]
2025-04-19 MCU power and signal routing
    [heli_avionics.kicad_pcb]
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2025-04-19 Finished off signal routing, also silkscreen fixes
    [heli_avionics.kicad_pcb]
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2025-04-22 Fix via clearance and copper annuli
    [heli_avionics.kicad_pcb]
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2025-04-25 Added soldermask expansion on pressure sensor
    [heli_avionics.kicad_pcb]
2025-04-27 Fixed most DRC errors
    Had to modify some footprints
    [heli_avionics.kicad_pcb, heli_avionics.kicad_sch]
2025-05-02 Added 3d model for chassis led connector
    [BMP390L.step, heli_avionics.kicad_pcb, heli_avionics.kicad_sch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]
2025-05-02 Added 3d model for reset pushbutton
    [User Library-Pushbutton3x4x2.step, heli_avionics.kicad_pcb]
2025-05-03 Experiment to see if 3rd motor driver is possible
    [heli_avionics.kicad_pcb, motors.kicad_sch]
2025-05-04 Finalise schematic to include 3rd motor driver
    [heli_avionics.kicad_sch, motors.kicad_sch]
2025-05-04 Correct pin ordering for 3rd motor driver
    [heli_avionics.kicad_pcb, heli_avionics.kicad_sch, motors.kicad_sch]
2025-05-05 Almost done with new motor driver layout
    [heli_avionics.kicad_pcb]
2025-05-06 Finished routing for 3rd motor driver
    [heli_avionics.kicad_pcb]
2025-05-08 Increased trace width to handle battery charging current
    [heli_avionics.kicad_pcb]
2025-05-08 Fixed ERC error for multi-function pin on bmp390
    [sensors.kicad_sch]
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2025-05-08 Fix pressure sensor 3d model
    [heli_avionics.kicad_pcb]
2025-05-09 Increased thermal relief spoke size on motor connections
    [heli_avionics.kicad_pcb]
2025-05-09 Increased B.Cu thermal pad size on motor drivers
    [heli_avionics.kicad_pcb]
2025-05-13 Fixed some unconnected tracks
    [heli_avionics.kicad_pcb]
2025-05-13 Fixed footprint DRC errors
    [heli_avionics.kicad_pcb, heli_avionics.kicad_sch]
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2025-05-29 Removed soldermask on back of motor driver thermal pads
    [heli_avionics.kicad_pcb]
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2025-05-30 Fixed fab layer
    [heli_avionics.kicad_pcb]
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2025-05-30 Made LED resistors bigger
    Physically, as in the footprint size
    [heli_avionics.kicad_pcb, heli_avionics.kicad_sch]
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2025-06-06 Added silkscreen decoration
    Decided not to go with the pictures but I have still included the footprint files in the commit
    [heli_avionics.kicad_pcb]
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2025-10-04 Trying to fix pwm
    [main.cpp]
2025-10-06 Fixing motor drivers
2025-10-18 Fixed motor issues
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
